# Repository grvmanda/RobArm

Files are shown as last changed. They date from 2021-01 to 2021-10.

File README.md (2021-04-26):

# RobArm

potential 6 DOF (maybe lower) 3D printed robotic arm. 

The repo is very rudimentary at the moment (CAD stored on Fusion 360's cloud); the code is based on ROS melodic.
The target platform is RPi4.

Custom stepper motor driver board (and boards for limit switches) designed on KiCad are also stored on this repo.

preview of rev 1 driver board: 

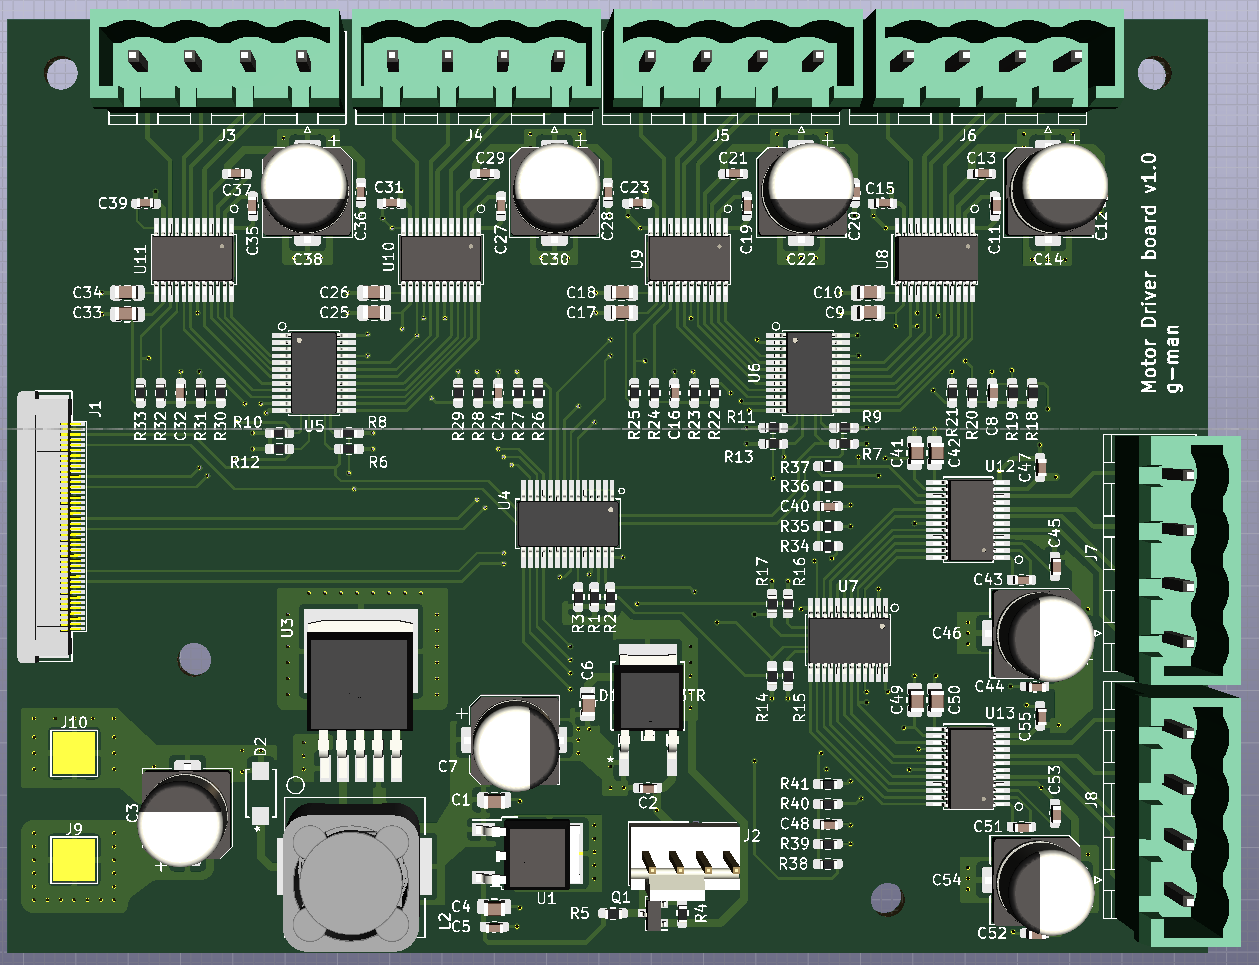
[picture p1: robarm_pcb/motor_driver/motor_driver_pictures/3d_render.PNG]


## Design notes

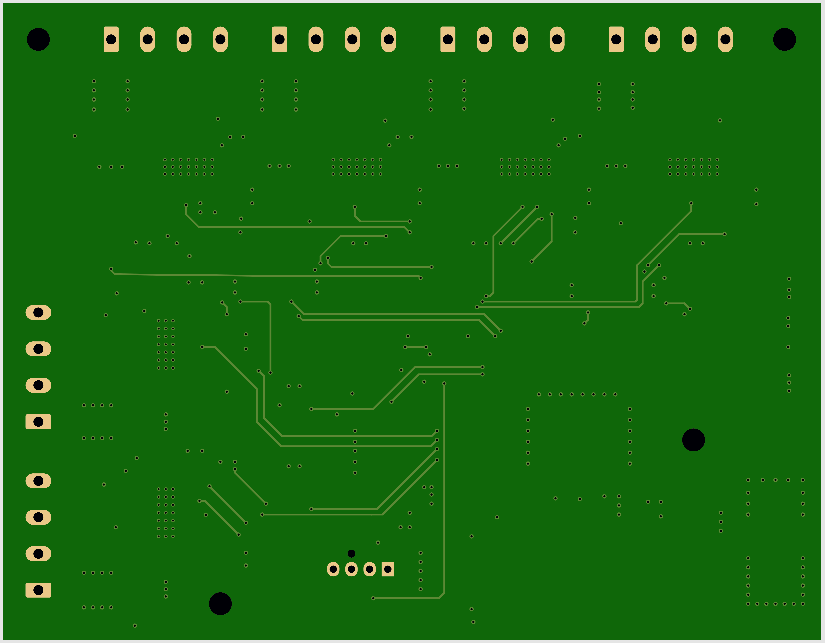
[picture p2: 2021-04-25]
robarm_pcb/motor_driver/motor_driver_pictures/back.PNG

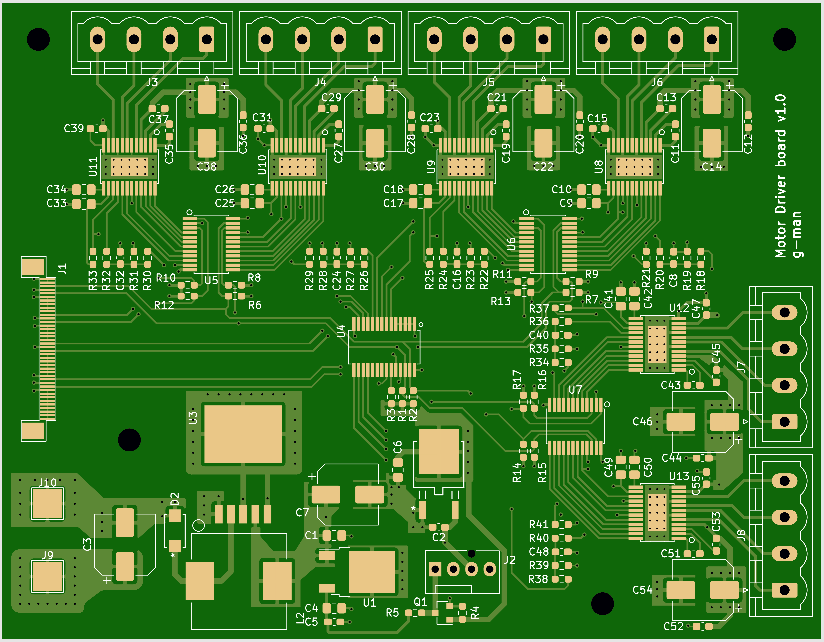
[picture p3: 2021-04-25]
robarm_pcb/motor_driver/motor_driver_pictures/front.PNG

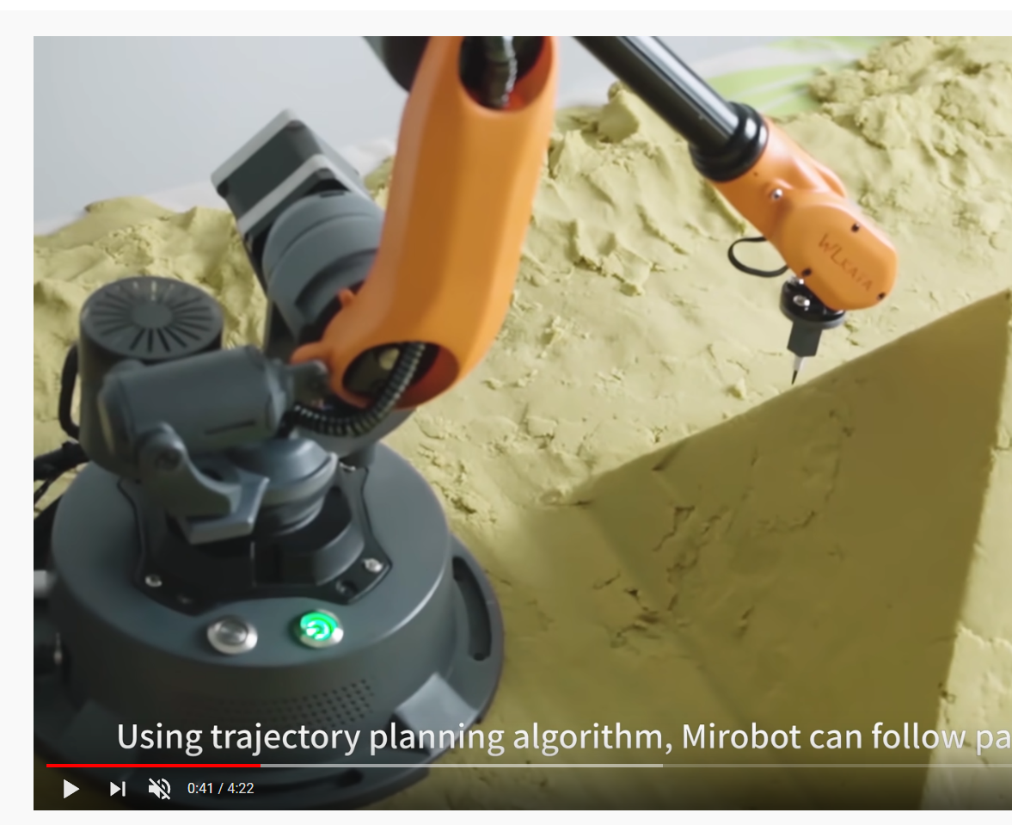
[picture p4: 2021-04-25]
robarm_documents/good reads/mirobot.png

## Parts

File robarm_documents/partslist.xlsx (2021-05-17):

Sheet: Template
 |  |  | Total |  | $0.00
Part Function | Part Number | Description | Unit Cost | Quantity | Total Cost | Link

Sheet: Motor Driver PCB
 |  |  | Total |  | $102.20
Part Function | Part Number | Description | Unit Cost | Quantity | Total Cost | Link
Power Management
12V PMIC | LM2576S-12/NOPB-ND | IC REG BUCK 12V 3A TO263-5 | $2.94 | 2 | $5.88 | https://www.digikey.com/en/products/detail/texas-instruments/LM2576S-12-NOPB/363651
3.3V PMIC | LD1117DT33TR | IC REG LINEAR 3.3V 800MA DPAK | $0.51 | 2 | $1.02 | https://www.digikey.com/en/products/detail/stmicroelectronics/LD1117DT33TR/585760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
5V | MC78M05BDTRKGOSCT-ND | IC REG LINEAR 5V 500MA DPAK | $0.53 | 2 | $1.06 | https://www.digikey.com/en/products/detail/on-semiconductor/MC78M05BDTRKG/919369
diodes | B340-13-F | DIODE SCHOTTKY 40V 3A SMC | $0.37 | 4 | $1.48 | https://www.digikey.com/en/products/detail/diodes-incorporated/B340-13-F/768768
Inductor for 3.3V PMIC | SRR1280A-101M | FIXED IND 100UH 2.1A 150MOHM SMD | $1.39 | 2 | $2.78 | https://www.digikey.com/en/products/detail/bourns-inc/SRR1280A-101M/4340250
 |  |  |  |  | $0.00
 |  |  |  |  | $0.00
Other ICs |  |  |  |  | $0.00
IO expansion | 296-25130-1-ND | IC I/O EXPANDER I2C 16B TSSOP | $1.61 | 5 | $8.05 | https://www.digikey.com/en/products/detail/texas-instruments/TCA9539PWR/2139129
PWM expansion | 568-11925-1-ND | IC LED DRVR LIN DIM 25MA 28TSSOP | $2.40 | 2 | $4.80 | https://www.digikey.com/en/products/detail/nxp-usa-inc/PCA9685PW-118/2034325
motor drivers | 296-45437-1-ND | IC MTR DRV BIPOLR 8-37V 24HTSSOP | $3.76 | 8 | $22.56 | https://www.digikey.com/en/products/detail/texas-instruments/DRV8886PWPR/6695811
level shifter FET | BSS138CT-ND | MOSFET N-CH 50V 220MA SOT23-3 | $0.28 | 5 | $1.40 | https://www.digikey.com/en/products/detail/on-semiconductor/BSS138/244210
 |  |  |  |  | $0.00
 |  |  |  |  | $0.00
Capacitors |  |  |  |  | $0.00
Driver VM caps | A768KE107M1VLAE036 | CAP ALUM POLY 100UF 20% 35V SMD | $0.68 | 7 | $4.76 | https://www.digikey.com/en/products/detail/kemet/A768KE107M1VLAE036/13420090
3.3V PMIC Cap | RHS0J102MCN1GS | CAP ALUM POLY 1000UF 6.3V SMD | $1.14 | 2 | $2.28 | https://www.digikey.com/en/products/detail/nichicon/RHS0J102MCN1GS/2209464
0.1uF Cap (Generic) 0603 | C0603C104M5RACTU | CAP CER 0.1UF 50V X7R 0603 | $0.02 | 50 | $0.97 | https://www.digikey.com/en/products/detail/kemet/C0603C104M5RACTU/2199782
10uF Cap (Generic) 0805 | GRM21BR61H106KE43L | CAP CER 10UF 50V X5R 0805 | $0.26 | 10 | $2.64 | https://www.digikey.com/en/products/detail/murata-electronics/GRM21BR61H106KE43L/10326316
0.47uF Cap (Generic) 0805 | CL21B474KBFNNNG | CAP CER 0.47UF 50V X7R 0805 | $0.04 | 50 | $1.90 | https://www.digikey.com/en/products/detail/samsung-electro-mechanics/CL21B474KBFNNNG/3894539
0.01uF Cap (Generic) 0603 | 06035C103JAT2A | CAP CER 10000PF 50V X7R 0603 | $0.04 | 50 | $1.93 | https://www.digikey.com/en/products/detail/avx-corporation/06035C103JAT2A/1600025
0.022uF Cap (Generic) 0603 | CL10B223KB8NNNC | CAP CER 0.022UF 50V X7R 0603 | $0.02 | 50 | $1.01 | https://www.digikey.com/en/products/detail/samsung-electro-mechanics/CL10B223KB8NNNC/3886762
0.22uF Cap (Generic) 0603 | CC0603ZRY5V9BB224 | CAP CER 0.22UF 50V Y5V 0603 | $0.09 | 10 | $0.86 | https://www.digikey.com/en/products/detail/yageo/CC0603ZRY5V9BB224/5195237
 |  |  |  |  | $0.00
 |  |  |  |  | $0.00
Resistors |  |  |  |  | $0.00
1k Res (Generic) 0603 | RC0603JR-7W1KL | RES 1K OHM 5% 1/5W 0603 | $0.03 | 20 | $0.60 | https://www.digikey.com/en/products/detail/yageo/RC0603JR-7W1KL/12698826
10k Res (Generic) 0603 0.1W | CRGCQ0603F10K | CRGCQ 0603 10K 1% | $0.01 | 100 | $1.26 | https://www.digikey.com/en/products/detail/te-connectivity-passive-product/CRGCQ0603F10K/8576302
20k Res (Generic) 0603 0.1W | RC0603JR-0720KL | RES SMD 20K OHM 5% 1/10W 0603 | $0.01 | 100 | $0.80 | https://www.digikey.com/en/products/detail/yageo/RC0603JR-0720KL/726740
30k Res (Generic) 0603 0.1W | AC0603JR-0730KL | RES SMD 30K OHM 5% 1/10W 0603 | $0.01 | 100 | $0.97 | https://www.digikey.com/en/products/detail/yageo/AC0603JR-0730KL/5896432
 |  |  |  |  | $0.00
 |  |  |  |  | $0.00
Connectors, Misc |  |  |  |  | $0.00
Fan connector | 470533000 | CONN HEADER VERT 4POS 2.54MM | $0.48 | 2 | $0.96 | https://www.digikey.com/en/products/detail/molex/0470533000/3262217
FPC to RPI | ZF5S-40-01-T-WT | CONN FFC BOTTOM 40POS 0.50MM R/A | $2.55 | 4 | $10.20 | https://www.digikey.com/en/products/detail/samtec-inc/ZF5S-40-01-T-WT/4822887
FPC adapter board | 1528-1096-ND | FPC ADAPTER 50PIN 0.5MM PITCH | $2.95 | 2 | $5.90 | https://www.digikey.com/en/products/detail/adafruit-industries-llc/1492/5154671
4" FFC cable | AE11342-ND | CABLE FFC 40POS 0.50MM 4" | $2.25 | 1 | $2.25 | https://www.digikey.com/en/products/detail/assmann-wsw-components/AFFC-050-40-102-11/6570363
6" FFC cable | WM19594-ND | CABLE FFC 40POS 0.50MM 6" | $2.66 | 1 | $2.66 | https://www.digikey.com/en/products/detail/molex/0151660436/3281317
Optical Sensor | OR626-ND | SENSOR OPT SLOT PHOTOTRAN PCB MT | $3.08 | 2 | $6.16 | https://www.digikey.com/en/products/detail/omron-electronics-inc-emc-div/EE-SX1071/274425
base limit switch to board | WM15254-ND | PICOBLADE 3 CIRCUIT 150MM | $2.53 | 1 | $2.53 | https://www.digikey.com/en/products/detail/molex/0151340302/6198144?s=N4IgTCBcDaIIwFY4GYAsAGZ6IF0C%2BQA
Connector Header 3 pos | WM1732-ND | CONN HEADER VERT 3POS 1.25MM | $0.24 | 5 | $2.53 | https://www.digikey.com/en/products/detail/molex/0530470310/242854
 |  |  |  |  | $0.00
 |  |  |  |  | $0.00
 |  |  |  |  | $0.00
 |  |  |  |  | $0.00
 |  |  |  |  | $0.00
 |  |  |  |  | $0.00
 |  |  |  |  | $0.00

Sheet: TMC2130 Based Board
 |  |  | Total |  | $0.00
Part Function | Part Number | Description | Unit Cost | Quantity | Total Cost | Link

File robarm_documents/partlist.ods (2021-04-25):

 |  |  |  | Total | $125.53
Part Function | Part Number | Description | Unit Cost | Quantity | Total Cost | Link
Robot Base Mechanical, etc
Nema-17 | 17HS19-1684S-PG51 | Base motor | $29.46 | 1 | $29.46 | https://www.omc-stepperonline.com/nema-17-stepper-motor-bipolar-l48mm-w-gear-raio-511-planetary-gearbox-17hs19-1684s-pg51.html
Ball Bearing | 6806-2RS | 30mm x 42mm x 7mm (set of 2) | $6.49 | 1 | $6.49 | https://www.amazon.com/gp/product/B082PYMKLG/ref=ppx_yo_dt_b_asin_title_o00_s00?ie=UTF8&psc=1
Thrust Bearing | 51107 | 35mm x 52mm x 12mm (set of 2) | $9.99 | 1 | $9.99 | https://www.amazon.com/gp/product/B07G847G75/ref=ppx_yo_dt_b_asin_title_o00_s00?ie=UTF8&psc=1
Noctua fan | NF-A4x10 PWM | 40mm x 10mm | $13.95 | 1 | $13.95 | https://www.amazon.com/dp/B07DXRNYNX/ref=emc_b_5_t
 |  |  |  |  | $0.00
Robot Base Electrical
Base PCB
Phoenix connectors | 1753479, 1751086 | 0.2inch 4 pin male and female connectors (set of 10) | $8.88 | 1 | $8.88 | https://www.amazon.com/Willwin-4-Pin-5-08mm-Female-Terminal/dp/B07796625D
motor drivers | DRV8886 | IC MTR DRV BIPOLR 8-37V 24HTSSOP | $3.76 | 6 | $22.56 | https://www.digikey.com/en/products/detail/texas-instruments/DRV8886PWPR/6695811
IO expansion | TCA9539 | IC I/O EXPANDER I2C 16B TSSOP | $1.61 | 3 | $4.83 | https://www.digikey.com/en/products/detail/texas-instruments/TCA9539PWR/2139129
PWM expansion | PCA9685 | IC LED DRVR LIN DIM 25MA 28TSSOP | $2.40 | 1 | $2.40 | https://www.digikey.com/en/products/detail/nxp-usa-inc/PCA9685PW-118/2034325
3.3V PMIC | LM2576SX-3.3/NOPB | IC REG BUCK 3.3V 3A TO263-5 | $2.94 | 0 | $0.00 | https://www.digikey.com/en/products/detail/texas-instruments/LM2576SX-3-3-NOPB/366792
Driver VM caps | A768KE107M1VLAE036 | CAP ALUM POLY 100UF 20% 35V SMD | $0.68 | 7 | $4.76 | https://www.digikey.com/en/products/detail/kemet/A768KE107M1VLAE036/13420090
3.3V PMIC Cap | RHS0J102MCN1GS | CAP ALUM POLY 1000UF 6.3V SMD | $1.14 | 1 | $1.14 | https://www.digikey.com/en/products/detail/nichicon/RHS0J102MCN1GS/2209464
Inductor for 3.3V PMIC | SRR1280A-101M | FIXED IND 100UH 2.1A 150MOHM SMD | $1.39 | 1 | $1.39 | https://www.digikey.com/en/products/detail/bourns-inc/SRR1280A-101M/4340250
50-pin FPC board for RPI | 1528-1096-ND | FPC ADAPTER 50PIN 0.5MM PITCH | $2.95 | 1 | $2.95 | https://www.digikey.com/en/products/detail/adafruit-industries-llc/1492/5154671
FPC to RPI | ZF5S-40-01-T-WT | CONN FFC BOTTOM 40POS 0.50MM R/A | $2.55 | 2 | $5.10 | https://www.digikey.com/en/products/detail/samtec-inc/ZF5S-40-01-T-WT/4822887
12V PMIC | LM2576S-12/NOPB-ND | IC REG BUCK 12V 3A TO263-5 | $2.94 | 0 | $0.00 | https://www.digikey.com/en/products/detail/texas-instruments/LM2576S-12-NOPB/363651
5V | MC78M05BDTRKG | IC REG LINEAR 5V 500MA DPAK | $0.49 | 1 | $0.49 | https://www.digikey.com/en/products/detail/on-semiconductor/MC78M05BDTRKG/919369
diodes | B340-13-F | DIODE SCHOTTKY 40V 3A SMC | $0.37 | 2 | $0.74 | https://www.digikey.com/en/products/detail/diodes-incorporated/B340-13-F/768768
3.3V PMIC | LD1117DT33TR | IC REG LINEAR 3.3V 800MA DPAK | $0.51 | 1 | $0.51 | https://www.digikey.com/en/products/detail/stmicroelectronics/LD1117DT33TR/585760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
Limit Switch PCB
Limit switch | D2FS-F-N-A | SWITCH SNAP ACT SPST-NO 100MA 6V |  |  | $0.00
Optical Sensor | OR626-ND | SENSOR OPT SLOT PHOTOTRAN PCB MT | $3.08 | 2 | $6.16 | https://www.digikey.com/en/products/detail/omron-electronics-inc-emc-div/EE-SX1071/274425
 |  |  |  |  | $0.00
Cable Assemblies
base limit switch to board | WM15254-ND | PICOBLADE 3 CIRCUIT 150MM | $2.53 | 1 | $2.53 | https://www.digikey.com/en/products/detail/molex/0151340302/6198144?s=N4IgTCBcDaIIwFY4GYAsAGZ6IF0C%2BQA
Connector Header 3 pos | WM1732-ND | CONN HEADER VERT 3POS 1.25MM | $0.24 | 5 | $1.20 | https://www.digikey.com/en/products/detail/molex/0530470310/242854
 |  |  |  |  | $0.00
 |  |  |  |  | $0.00
 |  |  |  |  | $0.00
 |  |  |  |  | $0.00
 |  |  |  |  | $0.00

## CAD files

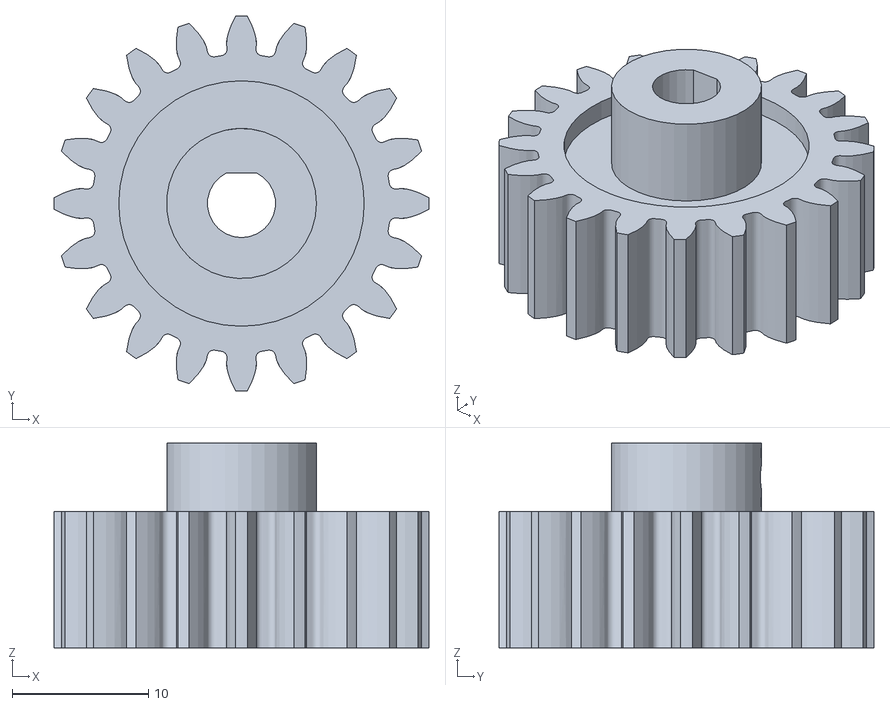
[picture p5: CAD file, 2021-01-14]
robarm_cad/nema17/second_draft.stl
27.5 x 27.5 x 15.0

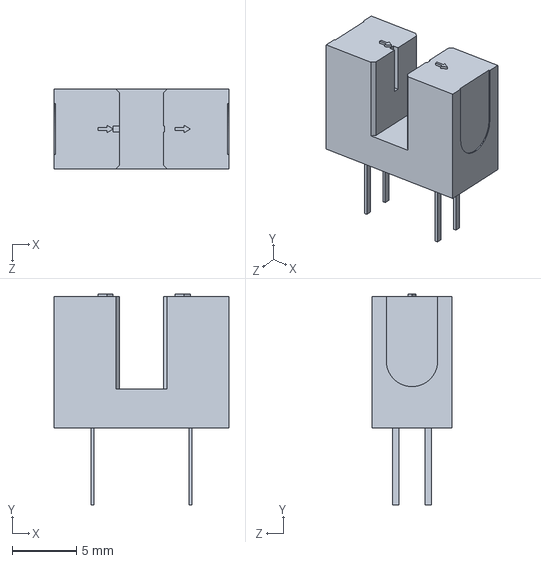
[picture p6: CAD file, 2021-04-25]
robarm_pcb/kicad_libraries/3dmodels/ul_EESX1071/STEP/EE_SX1071.step
13.6 x 16.4 x 6.20 mm

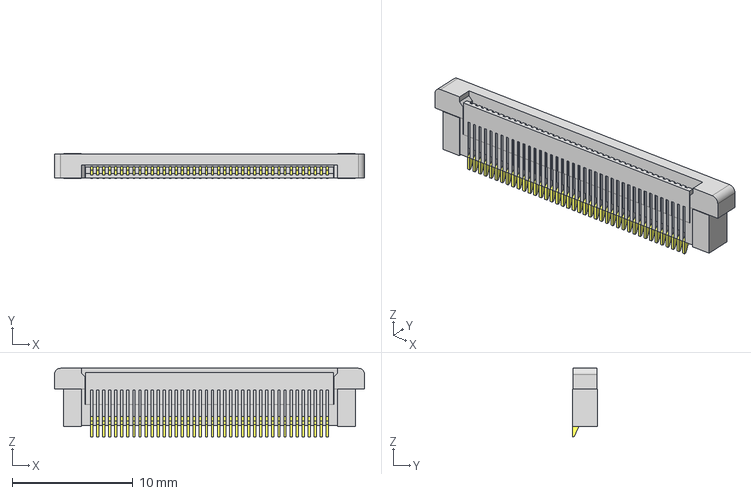
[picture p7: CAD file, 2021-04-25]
robarm_pcb/kicad_libraries/3dmodels/ZF5S-40-01-T-WT.stp
25.6 x 2.10 x 5.67 mm
_ZF5S-40-01-WT_socket
_C-297-40-01_pins

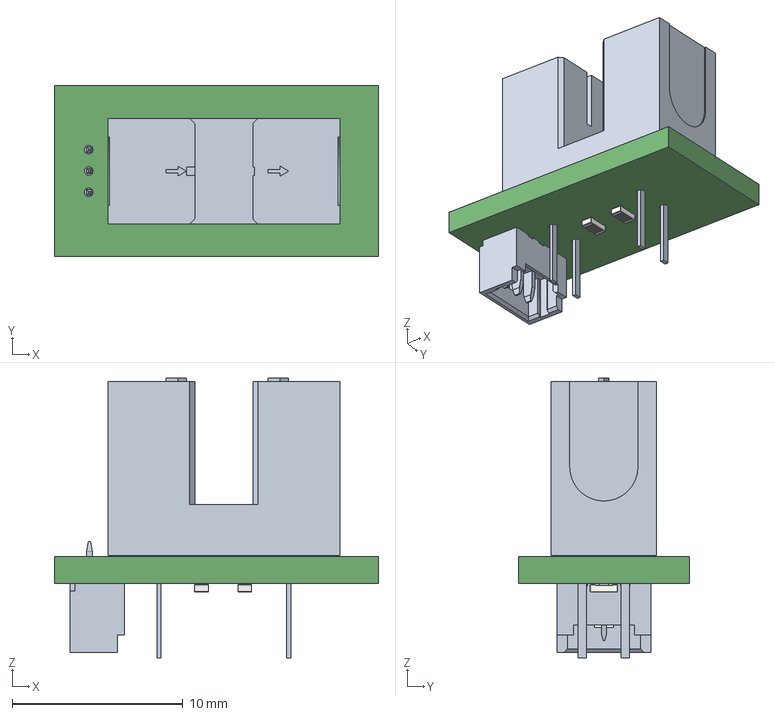
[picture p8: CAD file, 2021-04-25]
robarm_pcb/motor_driver/limit_switch_prj/limit_switch_prj/limit_switch_prj.step
19.0 x 10.0 x 16.4 mm

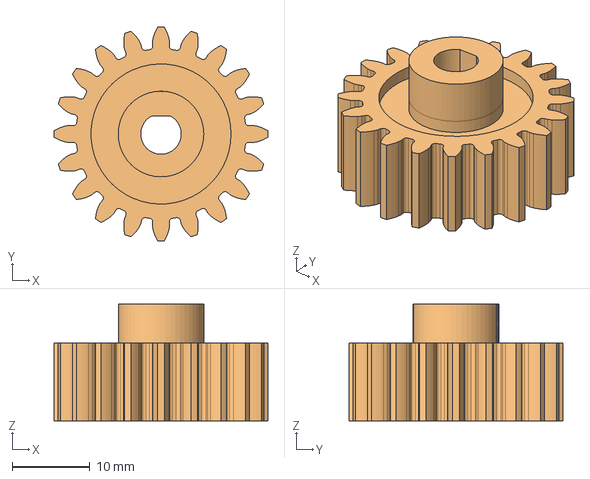
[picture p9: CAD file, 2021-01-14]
robarm_cad/nema17/spur_gear.FCStd
27.5 x 27.5 x 15.0 mm

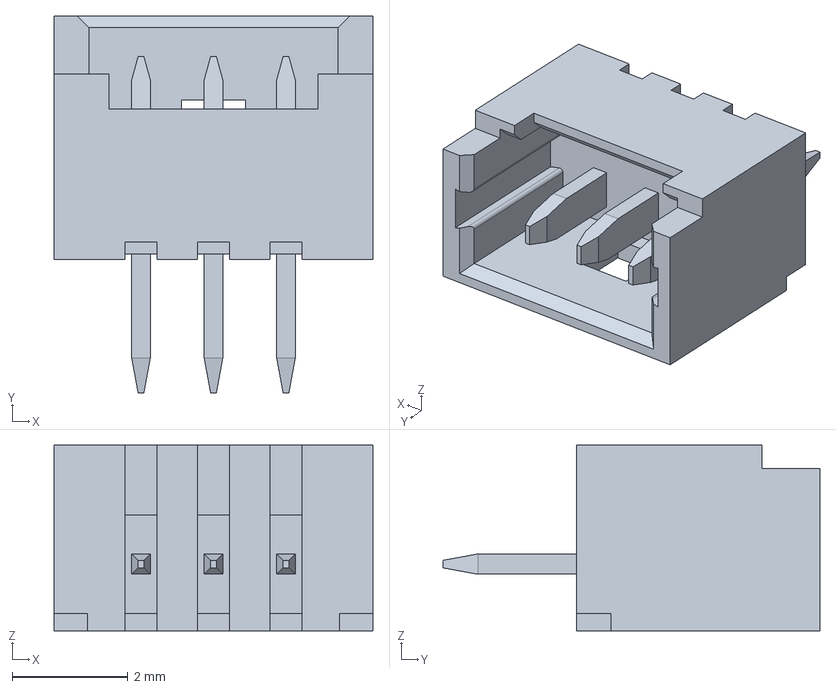
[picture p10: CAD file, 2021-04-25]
robarm_pcb/kicad_libraries/3dmodels/53047-0310_stp/530470310.stp
5.50 x 6.50 x 3.20 mm

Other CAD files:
robarm_pcb/motor_driver/limit_switch_prj/limit_switch_prj/limit_switch_prj v1.stl

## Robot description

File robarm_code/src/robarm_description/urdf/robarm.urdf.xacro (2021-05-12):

<?xml version="1.0"?>
<robot name="robarm" xmlns:xacro="http://ros.org/wiki/xacro">

  <!-- Import Rviz colors -->
  <xacro:include filename="$(find robarm_description)/urdf/materials.xacro" />

  <!-- Transmission macro -->
  <xacro:macro name="SimpleTransmission" params="joint n">
    <transmission name="tran${n}">
      <type>transmission_interface/SimpleTransmission</type>
      <joint name="${joint}">
        <hardwareInterface>hardware_interface/EffortJointInterface</hardwareInterface>
      </joint>
      <actuator name="motor${n}">
        <hardwareInterface>hardware_interface/EffortJointInterface</hardwareInterface>
        <mechanicalReduction>1</mechanicalReduction>
      </actuator>
    </transmission>
  </xacro:macro>

  <!-- World -->
  <link name="world">
  </link>

  <!-- World fixed joint-->
  <joint name="world_fixed" type="fixed">
    <origin xyz="0 0 0" rpy="0 0 0"/>
    <parent link="world"/>
    <child link="link1"/>
  </joint>

  <!-- Link 1 -->
  <link name="link1">
    <visual>
      <origin xyz="0 0 0.1" rpy="0 0 0"/>
      <!-- fix geometry later -->
      <geometry>
        <box size="0.4 0.4 0.2"/>
      </geometry>
      <material name="black"/>
    </visual>

    <collision>
      <origin xyz="0 0 0.1" rpy="0 0 0"/>
      <geometry>
        <cylinder radius="0.4" length="0.2"/>
      </geometry>
    </collision>

    <!-- inertia is not correct - change this later -->
    <inertial>
      <!-- <origin xyz="0 0 0" /> -->
      <mass value="0.1" />
      <inertia ixx="0.001" ixy="0.0" ixz="0.0" iyy="0.001" iyz="0.0" izz="0.001" />
    </inertial>
  </link>

  <!-- Joint 1 -->
  <joint name="joint1" type="revolute">
    <parent link="link1"/>
    <child link="link2"/>
    <origin xyz="0.0 0.0 0.2" rpy="0 0 0"/>
    <axis xyz="0 0 1"/>
    <limit velocity="4.8" effort="1" lower="${-pi*0.9}" upper="${pi*0.9}" />
  </joint>

  <!-- Transmission 1 -->
  <xacro:SimpleTransmission n="1" joint="joint1" />

  <!--  Link 2 -->
  <link name="link2">
    <visual>
      <origin xyz="0 0 0.3" rpy="0 0 0"/>
      <geometry>
        <box size="0.1 0.1 0.6"/>
      </geometry>
      <material name="orange"/>
    </visual>

    <collision>
      <origin xyz="0 0 0.6" rpy="0 0 0"/>
      <geometry>
        <cylinder radius="0.1" length="0.6"/>
      </geometry>
    </collision>

   <inertial>
      <!-- <origin xyz="0 0 0" /> -->
      <mass value="0.1" />
      <inertia ixx="0.001" ixy="0.0" ixz="0.0" iyy="0.001" iyz="0.0" izz="0.001" />
    </inertial>

  </link>

  <!-- Joint 2 -->
  <joint name="joint2" type="revolute">
    <parent link="link2"/>
    <child link="link3"/>
    <origin xyz="0.0 0.0 0.6" rpy="0 0 0"/>
    <axis xyz="0 1 0"/>
    <limit velocity="4.8" effort="1" lower="${-pi*0.9}" upper="${pi*0.9}" />
  </joint>

  <!-- Transmission 2 -->
  <xacro:SimpleTransmission n="2" joint="joint2" />

  <!--  Link 3 -->
  <link name="link3">
    <visual>
      <origin xyz="0 0 0.3" rpy="0 0 0"/>
      <geometry>
        <box size="0.1 0.1 0.6"/>
      </geometry>
      <material name="grey"/>
    </visual>

    <collision>
      <origin xyz="0 0 0.6" rpy="0 0 0"/>
      <geometry>
        <cylinder radius="0.1" length="0.6"/>
      </geometry>
    </collision>

   <inertial>
      <!-- <origin xyz="0 0 0" /> -->
      <mass value="0.1" />
      <inertia ixx="0.001" ixy="0.0" ixz="0.0" iyy="0.001" iyz="0.0" izz="0.001" />
    </inertial>

  </link>

  <!-- Joint 3 -->
  <joint name="joint3" type="revolute">
    <parent link="link3"/>
    <child link="link4"/>
    <origin xyz="0.0 0.0 0.6" rpy="0 0 0"/>
    <axis xyz="1 0 0"/>
    <limit velocity="4.8" effort="1" lower="${-pi*0.9}" upper="${pi*0.9}" />
  </joint>

  <!-- Transmission 3 -->
  <xacro:SimpleTransmission n="3" joint="joint3" />

  <!--  Link 4 -->
  <link name="link4">
    <visual>
      <origin xyz="0 0 0.3" rpy="0 0 0"/>
      <geometry>
        <box size="0.1 0.1 0.6"/>
      </geometry>
      <material name="brown"/>
    </visual>

    <collision>
      <origin xyz="0 0 0.6" rpy="0 0 0"/>
      <geometry>
        <cylinder radius="0.1" length="0.6"/>
      </geometry>
    </collision>

   <inertial>
      <!-- <origin xyz="0 0 0" /> -->
      <mass value="0.1" />
      <inertia ixx="0.00" ixy="0.0" ixz="0.0" iyy="0.001" iyz="0.0" izz="0.001" />
    </inertial>

  </link>

  <gazebo>
    <plugin name="gazebo_ros_control" filename="libgazebo_ros_control.so">
      <robotNamespace>/robarm</robotNamespace>
      <robotSimType>gazebo_ros_control/DefaultRobotHWSim</robotSimType>
    </plugin>
  </gazebo>
  
</robot>

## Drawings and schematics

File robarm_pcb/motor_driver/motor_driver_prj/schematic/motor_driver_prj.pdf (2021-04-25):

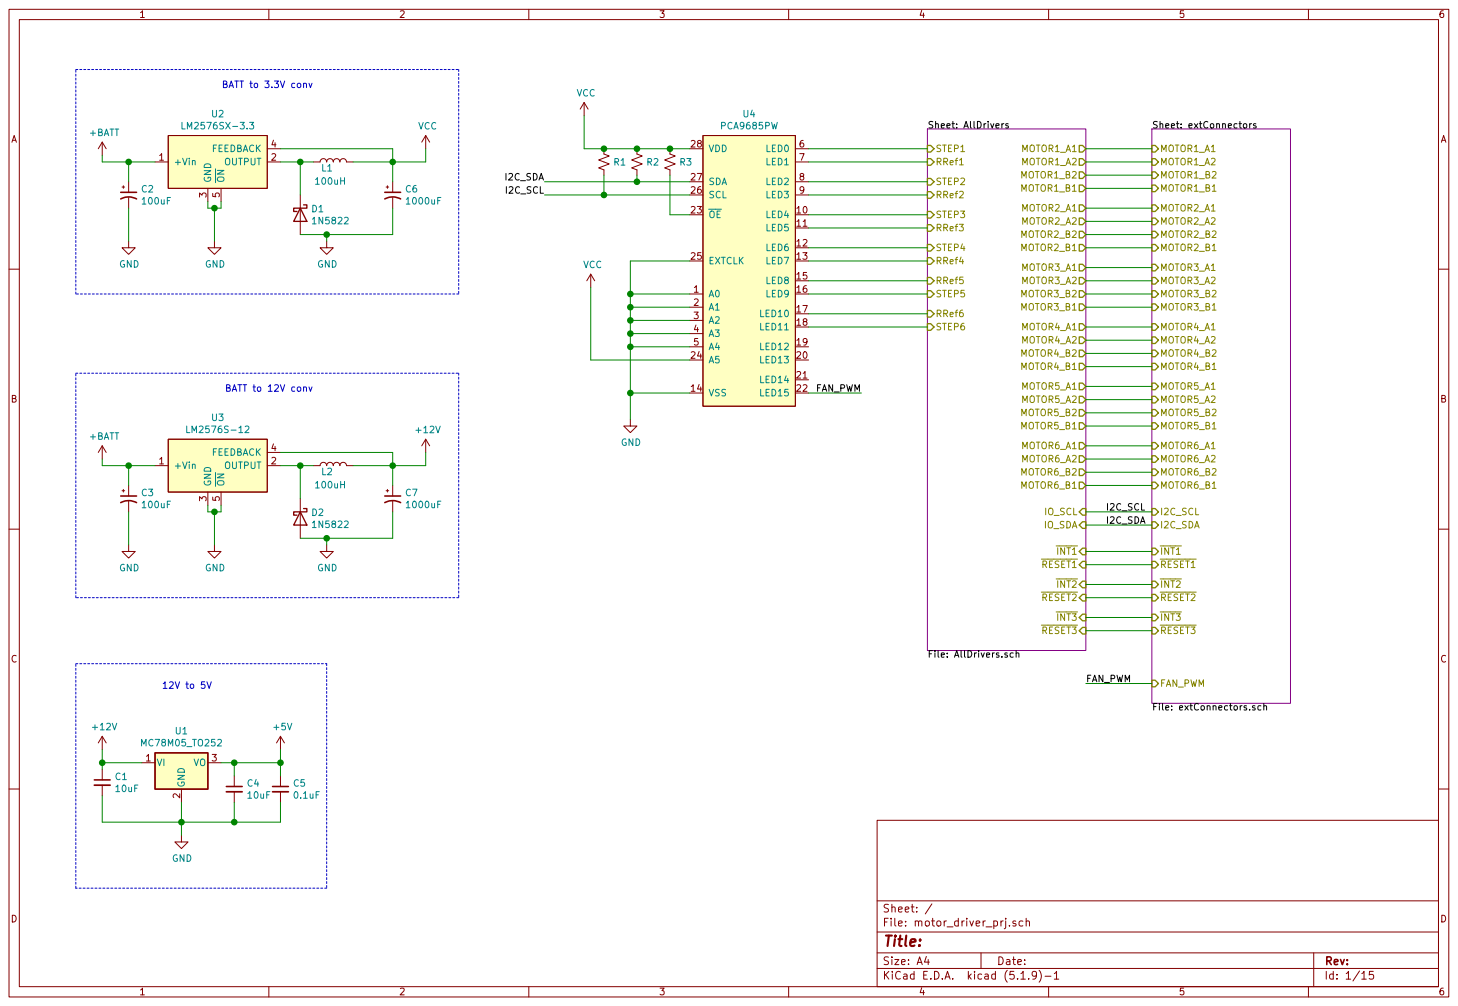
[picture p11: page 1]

Sheet: AllDrivers File: AllDrivers.sch
STEP1 RRef1 STEP2 RRef2 STEP3 RRef3 STEP4 RRef4 RRef6 STEP6 RRef5 STEP5

Sheet: extConnectors File: extConnectors.sch
MOTOR1_A1 MOTOR1_A2 MOTOR1_B2 MOTOR1_B1 MOTOR2_A1 MOTOR2_A2 MOTOR2_B2 MOTOR2_B1 MOTOR3_A1 MOTOR3_A2 MOTOR3_B2 MOTOR3_B1 MOTOR4_A1 MOTOR4_A2 MOTOR4_B2 MOTOR4_B1 MOTOR5_A1 MOTOR5_A2 MOTOR5_B2 MOTOR5_B1 MOTOR6_A1 MOTOR6_A2 MOTOR6_B2 MOTOR6_B1

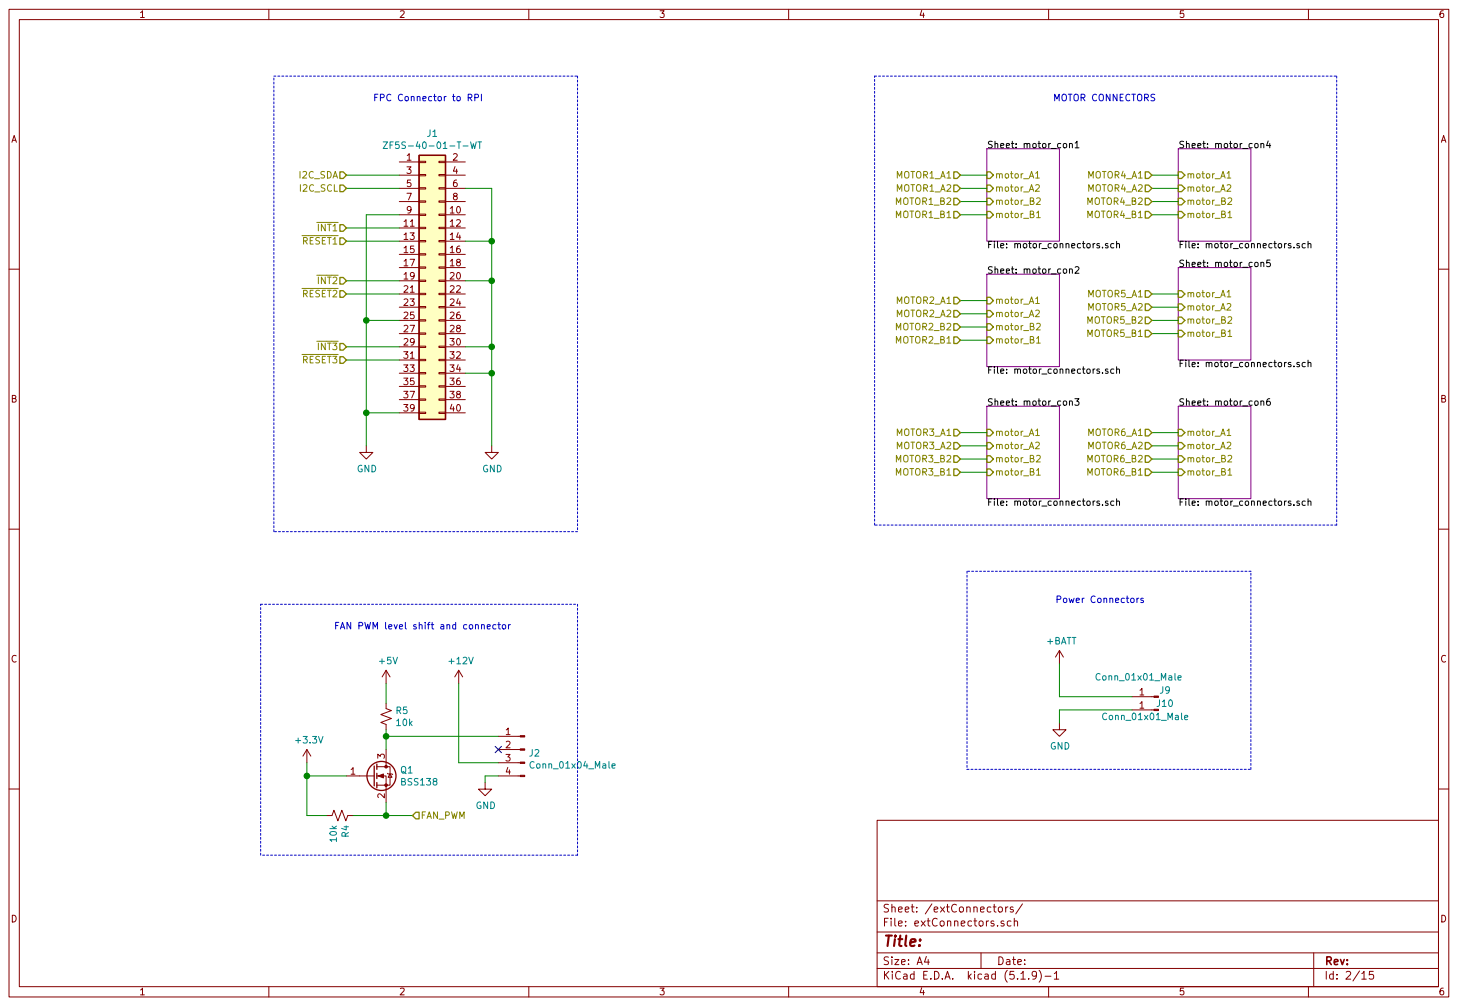
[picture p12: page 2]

Id: 2/15 Title: File: extConnectors.sch Sheet: /extConnectors/

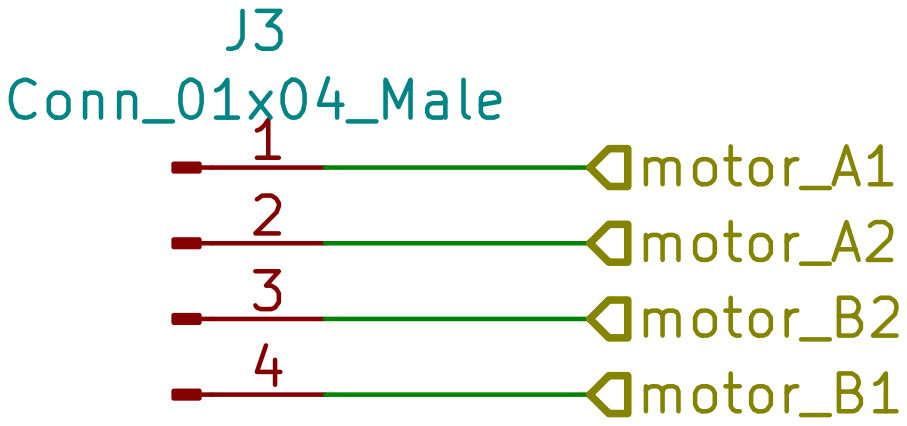
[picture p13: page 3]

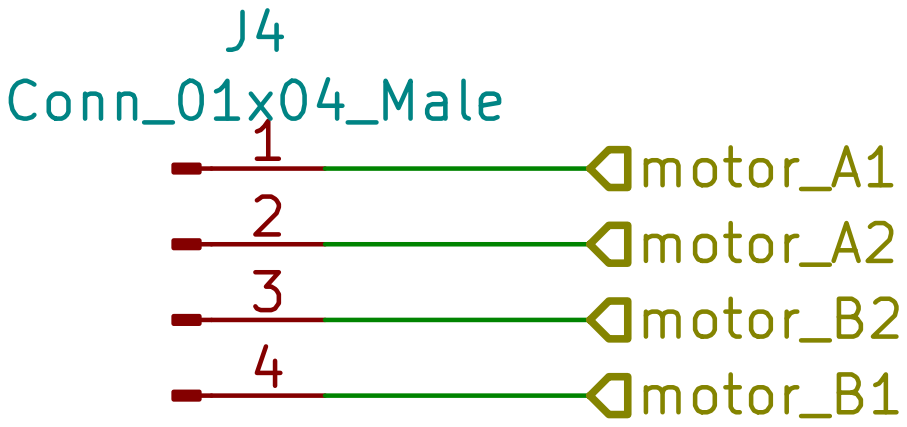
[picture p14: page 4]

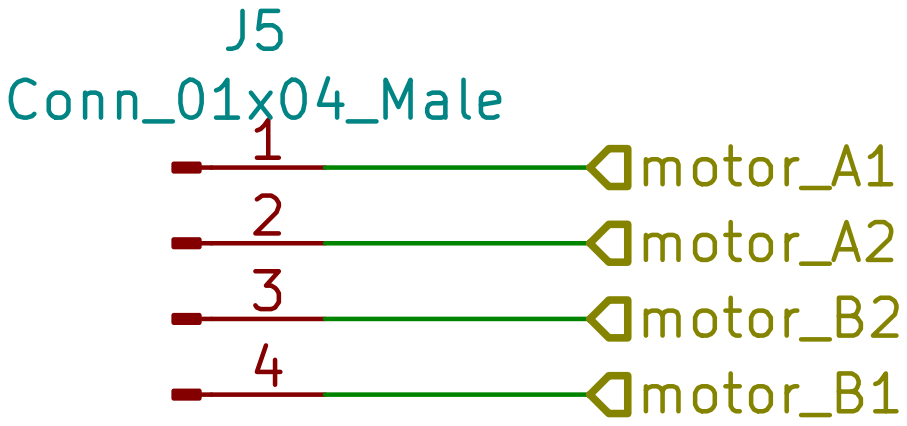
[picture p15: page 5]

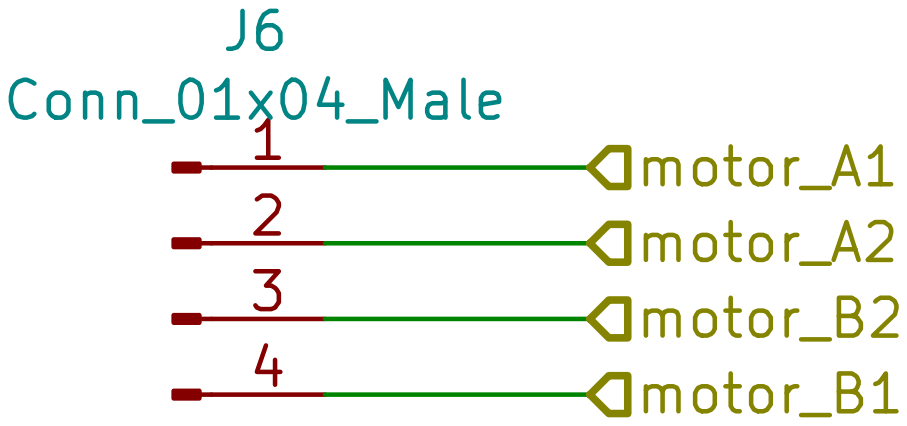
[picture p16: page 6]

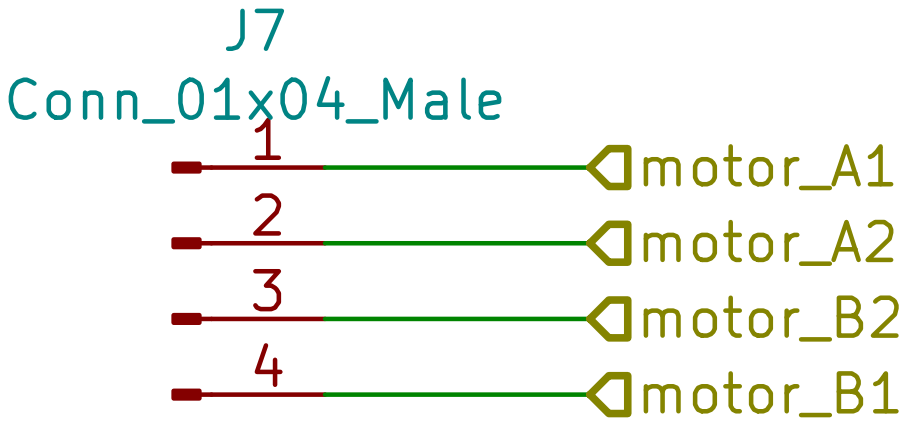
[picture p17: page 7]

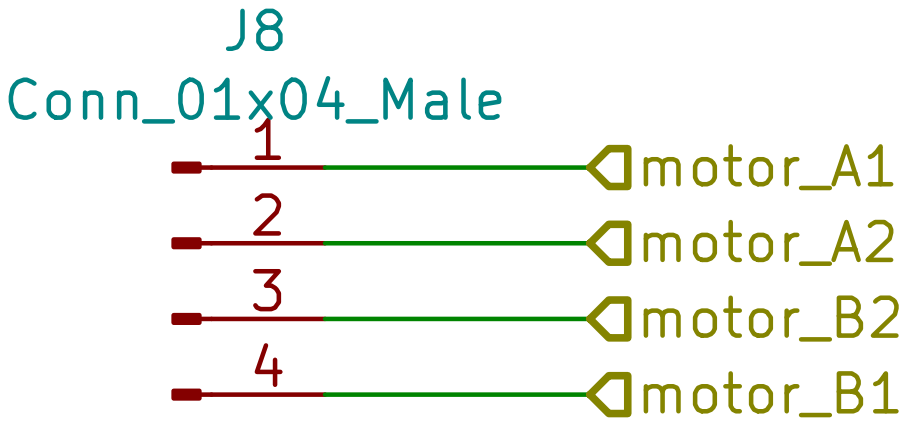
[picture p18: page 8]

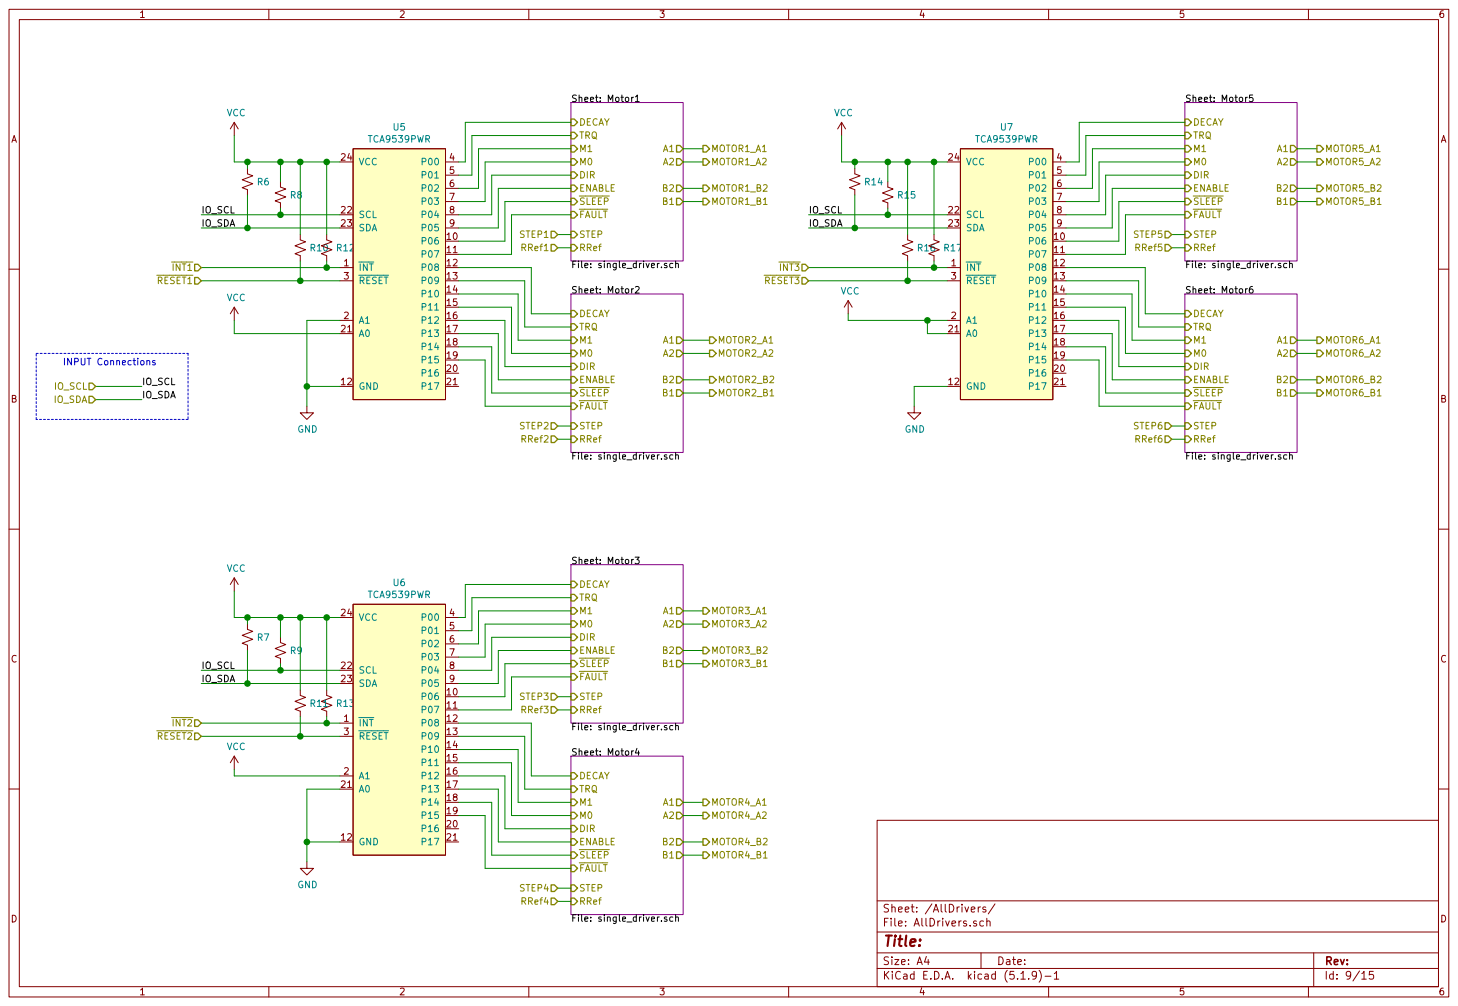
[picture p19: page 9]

A1A2B2B1 FAULT Sheet: Motor1 File: single_driver.sch RRef DECAY
TRQ M1 M0 DIR
A1A2B2B1 FAULT Sheet: Motor4 File: single_driver.sch RRef DECAY
A1A2B2B1 FAULT Sheet: Motor2 File: single_driver.sch RRef DECAY
A1A2B2B1 FAULT Sheet: Motor3 File: single_driver.sch RRef DECAY

Sheet: Motor5 File: single_driver.sch RRef DECAY
A1A2B2B1 FAULT Sheet: Motor6 File: single_driver.sch RRef DECAY

Id: 9/15 Title: File: AllDrivers.sch Sheet: /AllDrivers/

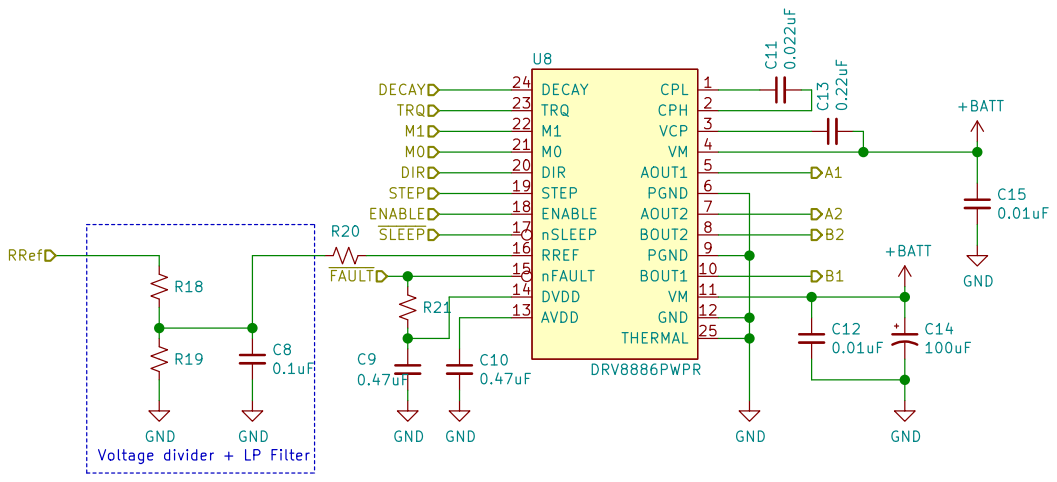
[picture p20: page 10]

File: single_driver.sch Sheet: /AllDrivers/Motor4/ GND

Voltage divider + LP Filter

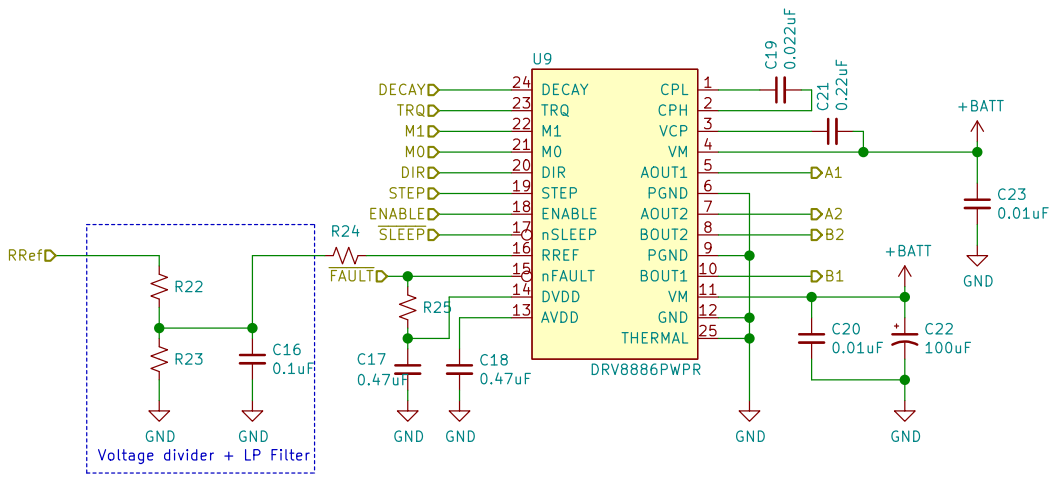
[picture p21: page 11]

File: single_driver.sch Sheet: /AllDrivers/Motor3/ GND

Voltage divider + LP Filter

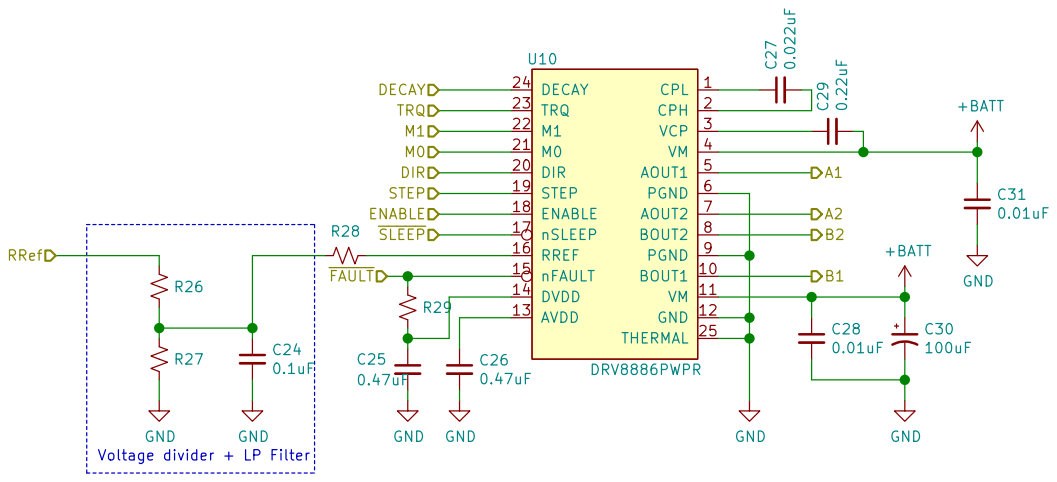
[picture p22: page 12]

File: single_driver.sch Sheet: /AllDrivers/Motor2/ GND

Voltage divider + LP Filter


File: single_driver.sch Sheet: /AllDrivers/Motor1/ GND

Voltage divider + LP Filter


File: single_driver.sch Sheet: /AllDrivers/Motor5/ GND

Voltage divider + LP Filter


File: single_driver.sch Sheet: /AllDrivers/Motor6/ GND

Voltage divider + LP Filter

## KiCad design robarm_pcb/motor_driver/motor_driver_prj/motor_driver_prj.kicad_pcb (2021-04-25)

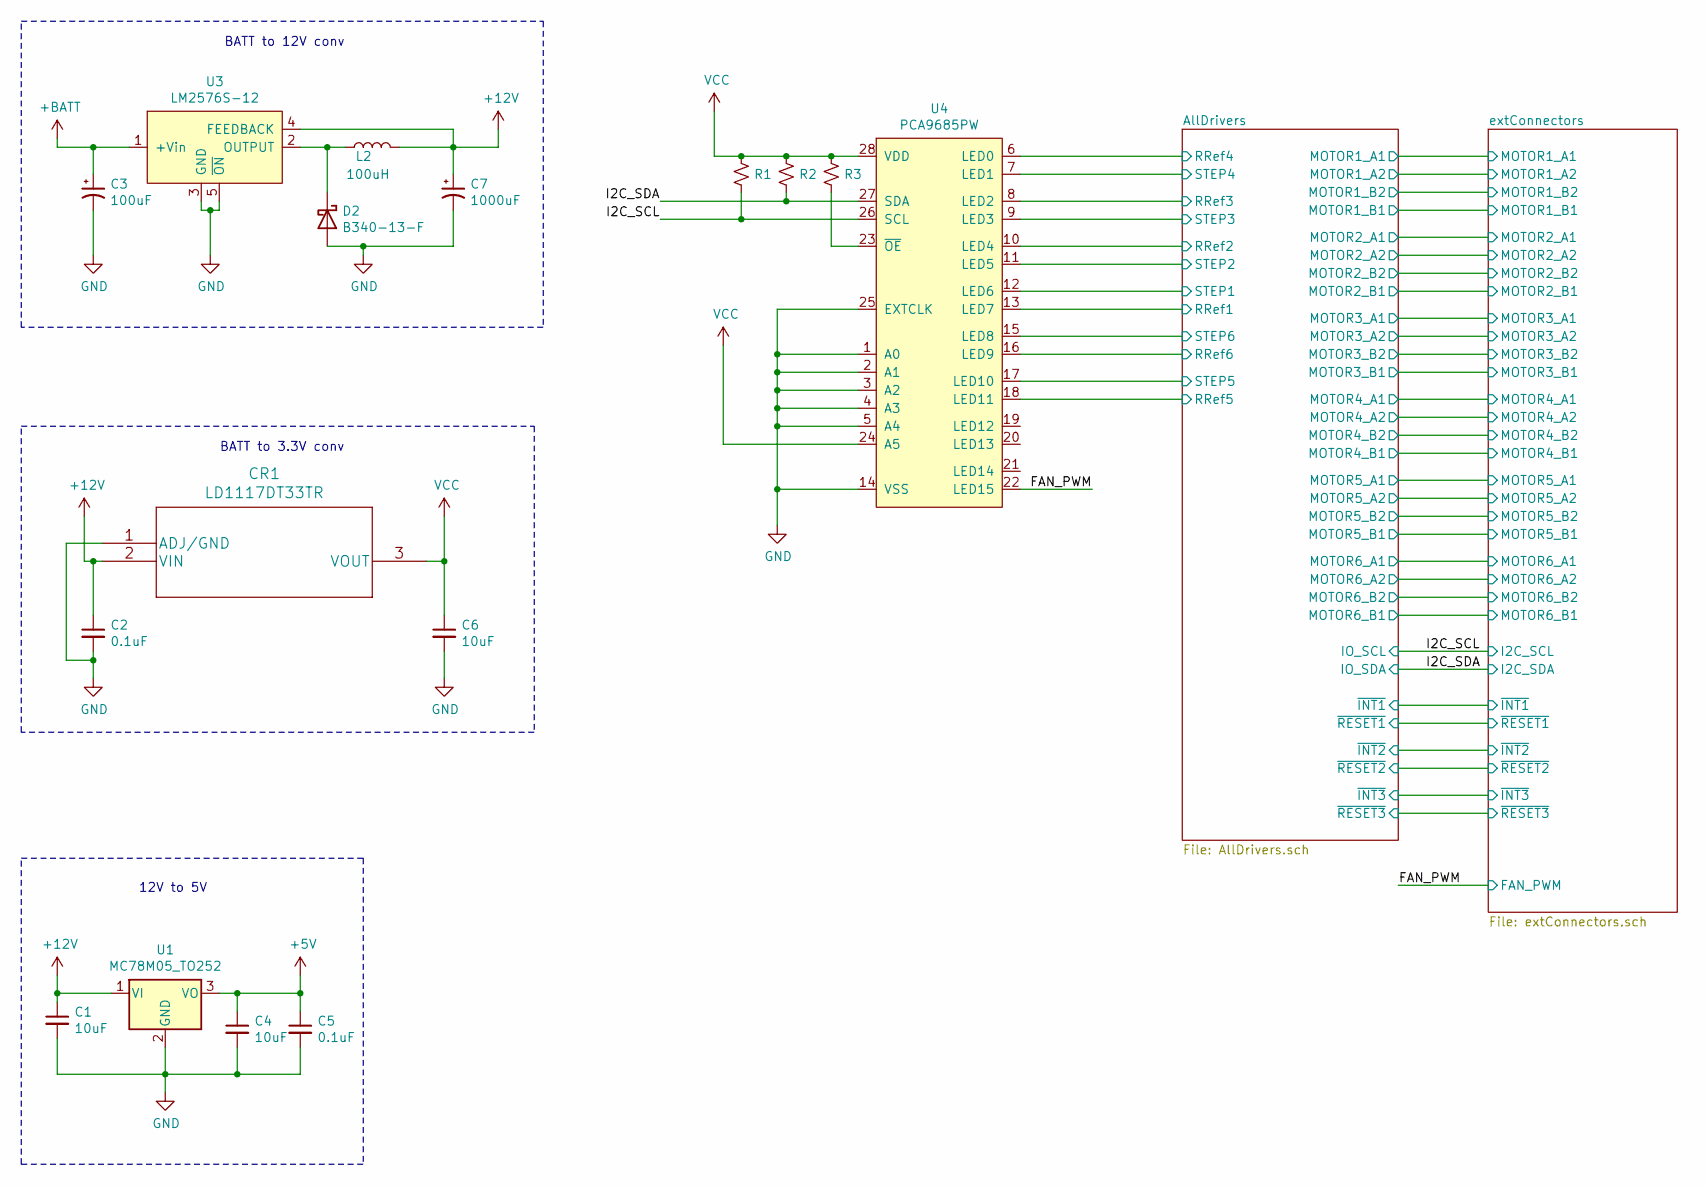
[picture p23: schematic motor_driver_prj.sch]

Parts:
C1, C4, C6: 10uF; C_0805_2012Metric_Pad1.18x1.45mm_HandSolder
C2, C5: 0.1uF; C_0603_1608Metric_Pad1.08x0.95mm_HandSolder
C3: 100uF; CP_Elec_8x6.2
C7: 1000uF; CP_Elec_8x6.2
CR1: LD1117DT33TR
D2: B340-13-F
L2: 100uH; SRR1280A-101M
R1, R2, R3: R_Small_US; R_0603_1608Metric_Pad0.98x0.95mm_HandSolder
U1: MC78M05_TO252; TO-252-2
U3: LM2576S-12; LM2576SX_TO263-5
U4: PCA9685PW; PC9685_TSSOP28

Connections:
+5V: C4.1, C5.1, U1.3 (VO); also elsewhere on the board
+12V: C1.1, C2.1, C7.1, CR1.2 (VIN), L2.2, U1.1 (VI), U3.4 (FEEDBACK); also elsewhere on the board
+BATT: C3.1, U3.1 (+Vin); also elsewhere on the board
/AllDrivers/RRef1: U4.13 (LED7); also elsewhere on the board
/AllDrivers/RRef2: U4.10 (LED4); also elsewhere on the board
/AllDrivers/RRef3: U4.8 (LED2); also elsewhere on the board
/AllDrivers/RRef4: U4.6 (LED0); also elsewhere on the board
/AllDrivers/RRef5: U4.18 (LED11); also elsewhere on the board
/AllDrivers/RRef6: U4.16 (LED9); also elsewhere on the board
/AllDrivers/STEP1: U4.12 (LED6); also elsewhere on the board
/AllDrivers/STEP2: U4.11 (LED5); also elsewhere on the board
/AllDrivers/STEP3: U4.9 (LED3); also elsewhere on the board
/AllDrivers/STEP4: U4.7 (LED1); also elsewhere on the board
/AllDrivers/STEP5: U4.17 (LED10); also elsewhere on the board
/AllDrivers/STEP6: U4.15 (LED8); also elsewhere on the board
/FAN_PWM: U4.22 (LED15); also elsewhere on the board
/I2C_SCL: R1.2, U4.26 (SCL); also elsewhere on the board
/I2C_SDA: R2.2, U4.27 (SDA); also elsewhere on the board
GND: C1.2, C2.2, C3.2, C4.2, C5.2, C6.2, C7.2, CR1.1 (ADJ/GND), D2.2 (A), U1.2 (GND), U3.3 (GND), U3.5 (~ON), U4.1 (A0), U4.2 (A1), U4.3 (A2), U4.4 (A3), U4.5 (A4), U4.14 (VSS), U4.25 (EXTCLK); also elsewhere on the board
unnamed: D2.1 (K), L2.1, U3.2 (OUTPUT)
unnamed: R3.2, U4.23 (~OE)
VCC: C6.1, CR1.3 (VOUT), R1.1, R2.1, R3.1, U4.24 (A5), U4.28 (VDD); also elsewhere on the board

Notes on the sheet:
BATT to 12V conv
12V to 5V
BATT to 3.3V conv

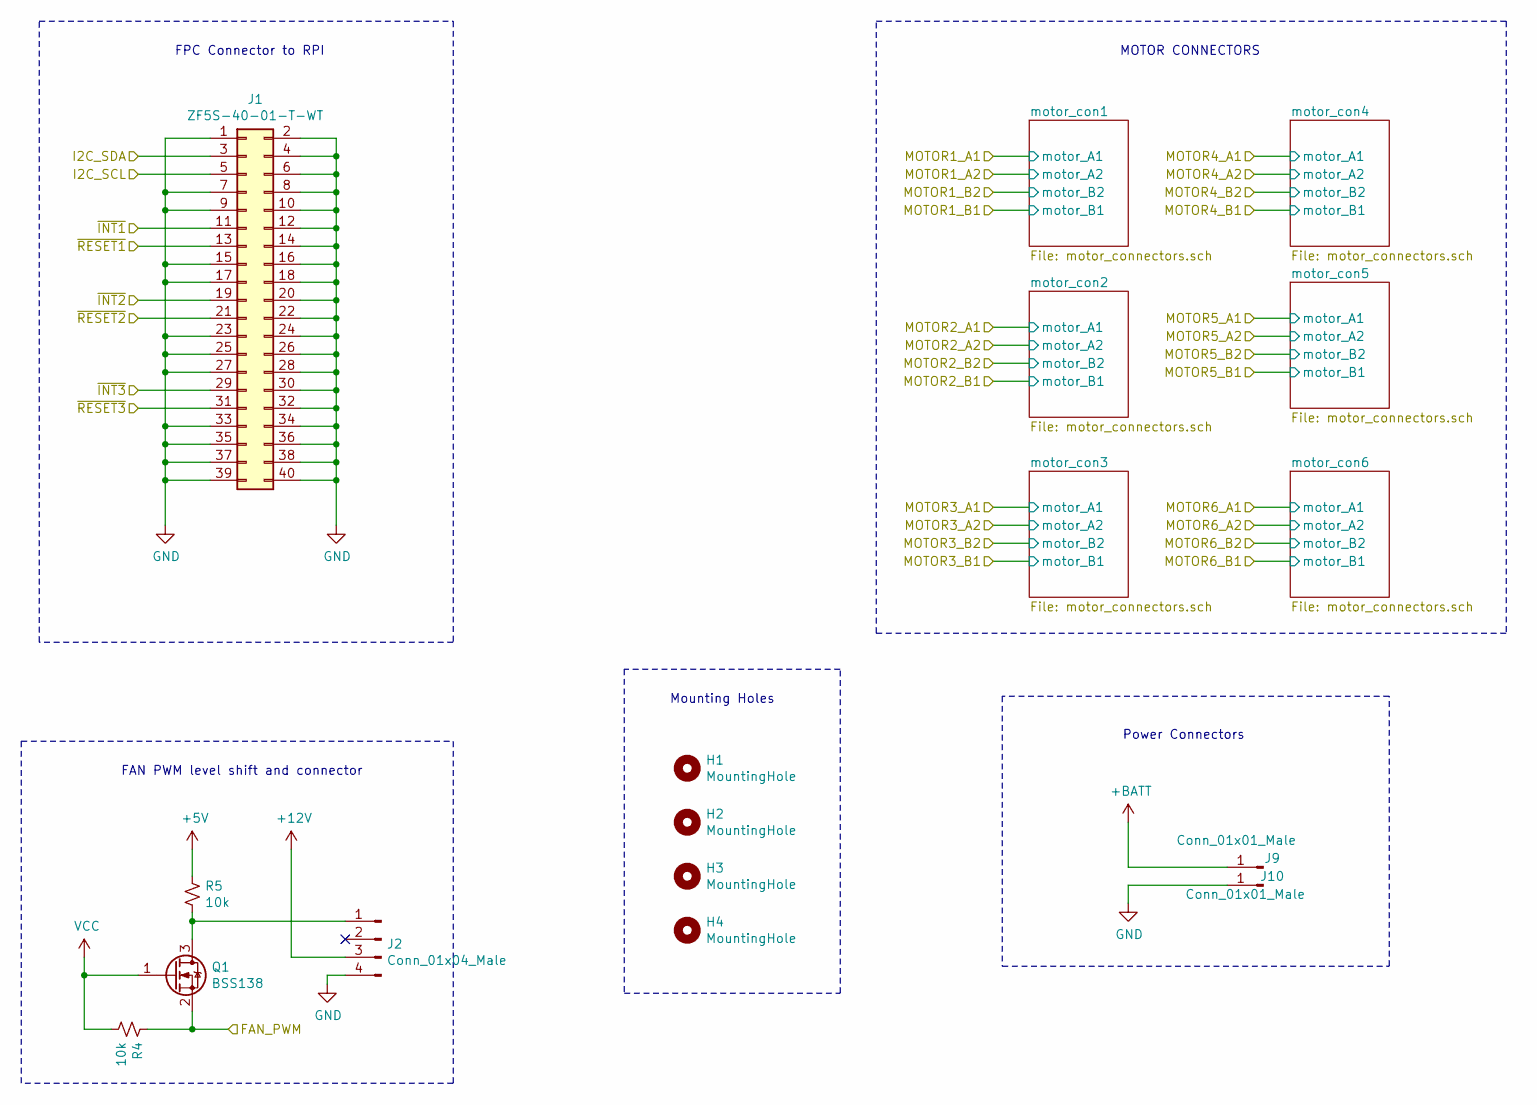
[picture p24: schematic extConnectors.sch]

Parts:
H1, H2, H3, H4: MountingHole; MountingHole_3.2mm_M3_ISO14580
J1: ZF5S-40-01-T-WT; FPC_40
J2: Conn_01x04_Male; FanPinHeader_1x04_P2.54mm_Vertical
J9, J10: Conn_01x01_Male; TestPoint_Pad_4.0x4.0mm
Q1: BSS138; SOT-23
R4, R5: 10k; R_0603_1608Metric_Pad0.98x0.95mm_HandSolder

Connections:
+5V: R5.1; also elsewhere on the board
+12V: J2.3; also elsewhere on the board
+BATT: J9.1; also elsewhere on the board
/AllDrivers/~INT1: J1.11; also elsewhere on the board
/AllDrivers/~INT2: J1.19; also elsewhere on the board
/AllDrivers/~INT3: J1.29; also elsewhere on the board
/AllDrivers/~RESET1: J1.13; also elsewhere on the board
/AllDrivers/~RESET2: J1.21; also elsewhere on the board
/AllDrivers/~RESET3: J1.31; also elsewhere on the board
/FAN_PWM: Q1.2 (S), R4.1; also elsewhere on the board
/I2C_SCL: J1.5; also elsewhere on the board
/I2C_SDA: J1.3; also elsewhere on the board
GND: J1.1, J1.2, J1.4, J1.6, J1.7, J1.8, J1.9, J1.10, J1.12, J1.14, J1.15, J1.16, J1.17, J1.18, J1.20, J1.22, J1.23, J1.24, J1.25, J1.26, J1.27, J1.28, J1.30, J1.32, J1.33, J1.34, J1.35, J1.36, J1.37, J1.38, J1.39, J1.40, J2.4, J10.1; also elsewhere on the board
unnamed: J2.1, Q1.3 (D), R5.2
VCC: Q1.1 (G), R4.2; also elsewhere on the board

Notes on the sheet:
MOTOR CONNECTORS
FPC Connector to RPI
FAN PWM level shift and connector
Power Connectors
Mounting Holes

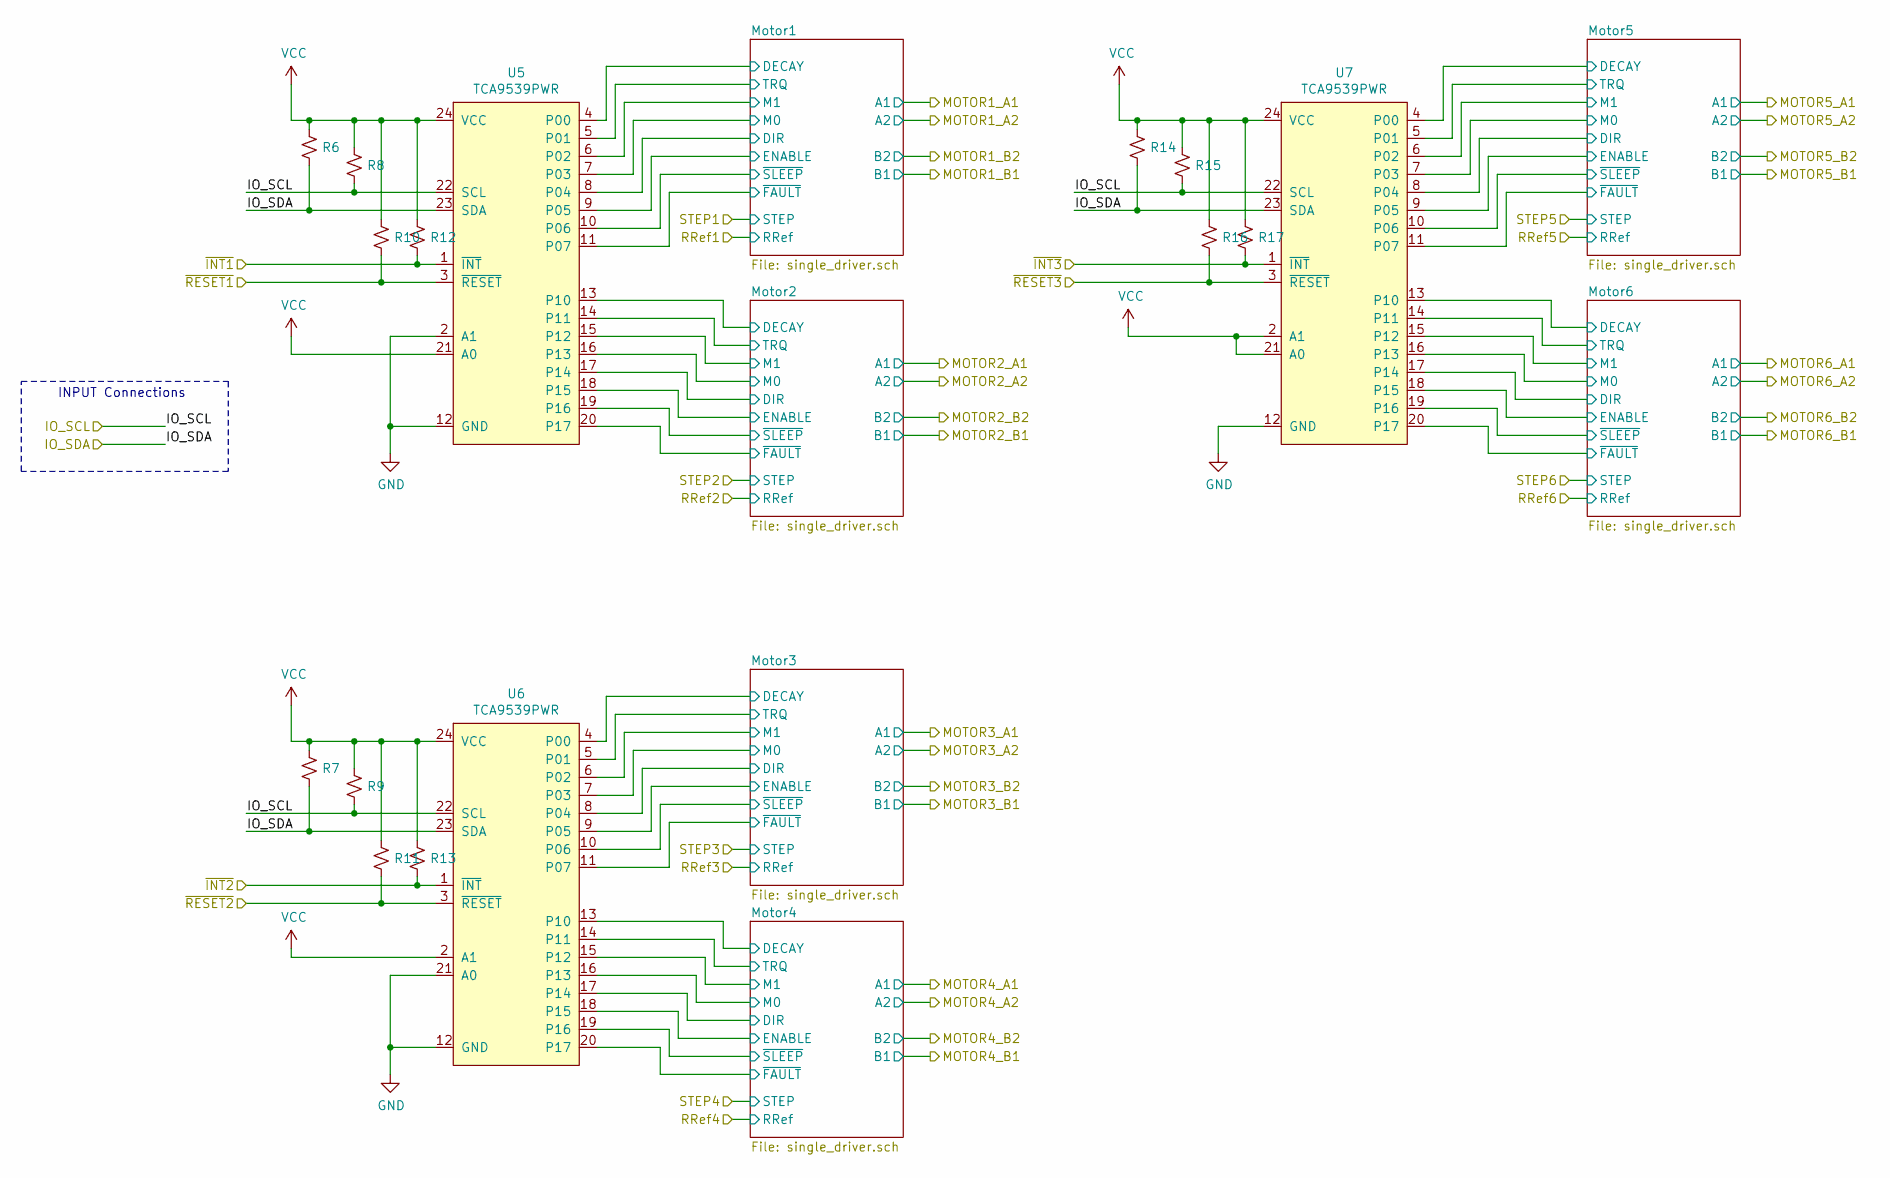
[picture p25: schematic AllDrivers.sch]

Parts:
R6, R7, R8, R9, R10, R11, R12, R13, R14, R15, R16, R17: 1; R_0603_1608Metric_Pad0.98x0.95mm_HandSolder
U5, U6, U7: TCA9539PWR; TCA9539_TSSOP-24

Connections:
/AllDrivers/Motor1/DECAY: U5.4 (P00); also elsewhere on the board
/AllDrivers/Motor1/DIR: U5.8 (P04); also elsewhere on the board
/AllDrivers/Motor1/ENABLE: U5.9 (P05); also elsewhere on the board
/AllDrivers/Motor1/M0: U5.7 (P03); also elsewhere on the board
/AllDrivers/Motor1/M1: U5.6 (P02); also elsewhere on the board
/AllDrivers/Motor1/TRQ: U5.5 (P01); also elsewhere on the board
/AllDrivers/Motor1/~FAULT: U5.11 (P07); also elsewhere on the board
/AllDrivers/Motor1/~SLEEP: U5.10 (P06); also elsewhere on the board
/AllDrivers/Motor2/DECAY: U5.13 (P10); also elsewhere on the board
/AllDrivers/Motor2/DIR: U5.17 (P14); also elsewhere on the board
/AllDrivers/Motor2/ENABLE: U5.18 (P15); also elsewhere on the board
/AllDrivers/Motor2/M0: U5.16 (P13); also elsewhere on the board
/AllDrivers/Motor2/M1: U5.15 (P12); also elsewhere on the board
/AllDrivers/Motor2/TRQ: U5.14 (P11); also elsewhere on the board
/AllDrivers/Motor2/~FAULT: U5.20 (P17); also elsewhere on the board
/AllDrivers/Motor2/~SLEEP: U5.19 (P16); also elsewhere on the board
/AllDrivers/Motor3/DECAY: U6.4 (P00); also elsewhere on the board
/AllDrivers/Motor3/DIR: U6.8 (P04); also elsewhere on the board
/AllDrivers/Motor3/ENABLE: U6.9 (P05); also elsewhere on the board
/AllDrivers/Motor3/M0: U6.7 (P03); also elsewhere on the board
/AllDrivers/Motor3/M1: U6.6 (P02); also elsewhere on the board
/AllDrivers/Motor3/TRQ: U6.5 (P01); also elsewhere on the board
/AllDrivers/Motor3/~FAULT: U6.11 (P07); also elsewhere on the board
/AllDrivers/Motor3/~SLEEP: U6.10 (P06); also elsewhere on the board
/AllDrivers/Motor4/DECAY: U6.13 (P10); also elsewhere on the board
/AllDrivers/Motor4/DIR: U6.17 (P14); also elsewhere on the board
/AllDrivers/Motor4/ENABLE: U6.18 (P15); also elsewhere on the board
/AllDrivers/Motor4/M0: U6.16 (P13); also elsewhere on the board
/AllDrivers/Motor4/M1: U6.15 (P12); also elsewhere on the board
/AllDrivers/Motor4/TRQ: U6.14 (P11); also elsewhere on the board
/AllDrivers/Motor4/~FAULT: U6.20 (P17); also elsewhere on the board
/AllDrivers/Motor4/~SLEEP: U6.19 (P16); also elsewhere on the board
/AllDrivers/Motor5/DECAY: U7.4 (P00); also elsewhere on the board
/AllDrivers/Motor5/DIR: U7.8 (P04); also elsewhere on the board
/AllDrivers/Motor5/ENABLE: U7.9 (P05); also elsewhere on the board
/AllDrivers/Motor5/M0: U7.7 (P03); also elsewhere on the board
/AllDrivers/Motor5/M1: U7.6 (P02); also elsewhere on the board
/AllDrivers/Motor5/TRQ: U7.5 (P01); also elsewhere on the board
/AllDrivers/Motor5/~FAULT: U7.11 (P07); also elsewhere on the board
/AllDrivers/Motor5/~SLEEP: U7.10 (P06); also elsewhere on the board
/AllDrivers/Motor6/DECAY: U7.13 (P10); also elsewhere on the board
/AllDrivers/Motor6/DIR: U7.17 (P14); also elsewhere on the board
/AllDrivers/Motor6/ENABLE: U7.18 (P15); also elsewhere on the board
/AllDrivers/Motor6/M0: U7.16 (P13); also elsewhere on the board
/AllDrivers/Motor6/M1: U7.15 (P12); also elsewhere on the board
/AllDrivers/Motor6/TRQ: U7.14 (P11); also elsewhere on the board
/AllDrivers/Motor6/~FAULT: U7.20 (P17); also elsewhere on the board
/AllDrivers/Motor6/~SLEEP: U7.19 (P16); also elsewhere on the board
/AllDrivers/~INT1: R12.2, U5.1 (~INT); also elsewhere on the board
/AllDrivers/~INT2: R13.2, U6.1 (~INT); also elsewhere on the board
/AllDrivers/~INT3: R17.2, U7.1 (~INT); also elsewhere on the board
/AllDrivers/~RESET1: R10.2, U5.3 (~RESET); also elsewhere on the board
/AllDrivers/~RESET2: R11.2, U6.3 (~RESET); also elsewhere on the board
/AllDrivers/~RESET3: R16.2, U7.3 (~RESET); also elsewhere on the board
/I2C_SCL: R8.2, R9.2, R15.2, U5.22 (SCL), U6.22 (SCL), U7.22 (SCL); also elsewhere on the board
/I2C_SDA: R6.2, R7.2, R14.2, U5.23 (SDA), U6.23 (SDA), U7.23 (SDA); also elsewhere on the board
GND: U5.2 (A1), U5.12 (GND), U6.12 (GND), U6.21 (A0), U7.12 (GND); also elsewhere on the board
VCC: R6.1, R7.1, R8.1, R9.1, R10.1, R11.1, R12.1, R13.1, R14.1, R15.1, R16.1, R17.1, U5.21 (A0), U5.24 (VCC), U6.2 (A1), U6.24 (VCC), U7.2 (A1), U7.21 (A0), U7.24 (VCC); also elsewhere on the board

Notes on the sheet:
INPUT Connections

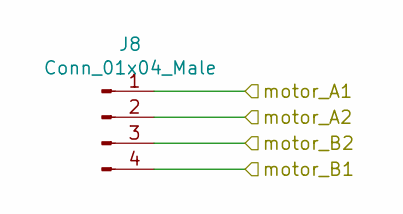
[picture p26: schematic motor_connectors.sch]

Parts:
J3: Conn_01x04_Male; PhoenixContact_MSTBVA_2,5_4-G-5,08_1x04_P5.08mm_Vertical

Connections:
/AllDrivers/MOTOR1_A1: J3.1; also elsewhere on the board
/AllDrivers/MOTOR1_A2: J3.2; also elsewhere on the board
/AllDrivers/MOTOR1_B1: J3.4; also elsewhere on the board
/AllDrivers/MOTOR1_B2: J3.3; also elsewhere on the board

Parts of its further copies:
J4, J5, J6, J7, J8: Conn_01x04_Male; PhoenixContact_MSTBVA_2,5_4-G-5,08_1x04_P5.08mm_Vertical

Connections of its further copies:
/AllDrivers/MOTOR2_A1: J4.1; also elsewhere on the board
/AllDrivers/MOTOR2_A2: J4.2; also elsewhere on the board
/AllDrivers/MOTOR2_B1: J4.4; also elsewhere on the board
/AllDrivers/MOTOR2_B2: J4.3; also elsewhere on the board
/AllDrivers/MOTOR3_A1: J5.1; also elsewhere on the board
/AllDrivers/MOTOR3_A2: J5.2; also elsewhere on the board
/AllDrivers/MOTOR3_B1: J5.4; also elsewhere on the board
/AllDrivers/MOTOR3_B2: J5.3; also elsewhere on the board
/AllDrivers/MOTOR4_A1: J6.1; also elsewhere on the board
/AllDrivers/MOTOR4_A2: J6.2; also elsewhere on the board
/AllDrivers/MOTOR4_B1: J6.4; also elsewhere on the board
/AllDrivers/MOTOR4_B2: J6.3; also elsewhere on the board
/AllDrivers/MOTOR5_A1: J7.1; also elsewhere on the board
/AllDrivers/MOTOR5_A2: J7.2; also elsewhere on the board
/AllDrivers/MOTOR5_B1: J7.4; also elsewhere on the board
/AllDrivers/MOTOR5_B2: J7.3; also elsewhere on the board
/AllDrivers/MOTOR6_A1: J8.1; also elsewhere on the board
/AllDrivers/MOTOR6_A2: J8.2; also elsewhere on the board
/AllDrivers/MOTOR6_B1: J8.4; also elsewhere on the board
/AllDrivers/MOTOR6_B2: J8.3; also elsewhere on the board

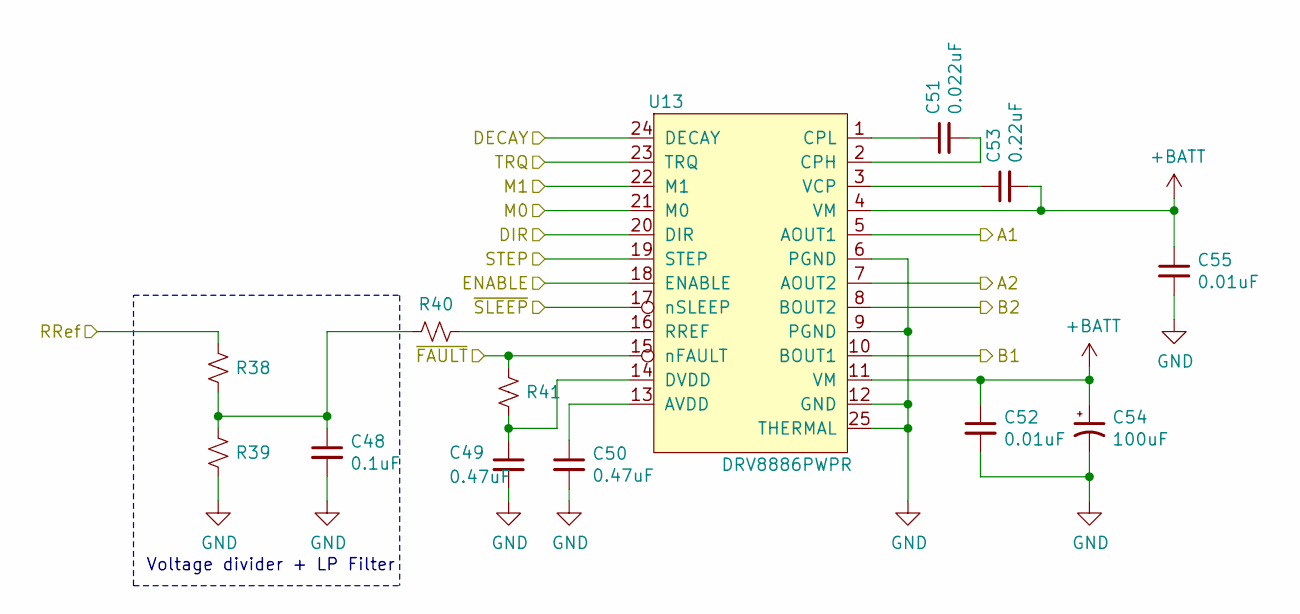
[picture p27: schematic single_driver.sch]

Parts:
C8: 0.1uF; C_0603_1608Metric_Pad1.08x0.95mm_HandSolder
C9, C10: 0.47uF; C_0805_2012Metric_Pad1.18x1.45mm_HandSolder
C11: 0.022uF; C_0603_1608Metric_Pad1.08x0.95mm_HandSolder
C12, C15: 0.01uF; C_0603_1608Metric_Pad1.08x0.95mm_HandSolder
C13: 0.22uF; C_0603_1608Metric_Pad1.08x0.95mm_HandSolder
C14: 100uF; CP_Elec_8x6.2
R18, R19, R21: R_Small_US; R_0603_1608Metric_Pad0.98x0.95mm_HandSolder
R20: rref; R_0603_1608Metric_Pad0.98x0.95mm_HandSolder
U8: DRV8886PWPR‎; DRV8886_HTSSOP-24

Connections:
+BATT: C12.1, C13.2, C14.1, C15.1, U8.4 (VM), U8.11 (VM); also elsewhere on the board
/AllDrivers/MOTOR4_A1: U8.5 (AOUT1); also elsewhere on the board
/AllDrivers/MOTOR4_A2: U8.7 (AOUT2); also elsewhere on the board
/AllDrivers/MOTOR4_B1: U8.10 (BOUT1); also elsewhere on the board
/AllDrivers/MOTOR4_B2: U8.8 (BOUT2); also elsewhere on the board
/AllDrivers/Motor4/DECAY: U8.24 (DECAY); also elsewhere on the board
/AllDrivers/Motor4/DIR: U8.20 (DIR); also elsewhere on the board
/AllDrivers/Motor4/ENABLE: U8.18 (ENABLE); also elsewhere on the board
/AllDrivers/Motor4/M0: U8.21 (M0); also elsewhere on the board
/AllDrivers/Motor4/M1: U8.22 (M1); also elsewhere on the board
/AllDrivers/Motor4/TRQ: U8.23 (TRQ); also elsewhere on the board
/AllDrivers/Motor4/~FAULT: R21.1, U8.15 (nFAULT); also elsewhere on the board
/AllDrivers/Motor4/~SLEEP: U8.17 (nSLEEP); also elsewhere on the board
/AllDrivers/RRef4: R18.1; also elsewhere on the board
/AllDrivers/STEP4: U8.19 (STEP); also elsewhere on the board
GND: C8.2, C9.2, C10.2, C12.2, C14.2, C15.2, R19.2, U8.6 (PGND), U8.9 (PGND), U8.12 (GND), U8.25 (THERMAL); also elsewhere on the board
unnamed: C8.1, R18.2, R19.1, R20.1
unnamed: C9.1, R21.2, U8.14 (DVDD)
unnamed: C10.1, U8.13 (AVDD)
unnamed: C11.1, U8.1 (CPL)
unnamed: C11.2, U8.2 (CPH)
unnamed: C13.1, U8.3 (VCP)
unnamed: R20.2, U8.16 (RREF)

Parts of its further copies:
C16, C24, C32, C40, C48: 0.1uF; C_0603_1608Metric_Pad1.08x0.95mm_HandSolder
C17, C18, C25, C26, C33, C34, C41, C42, C49, C50: 0.47uF; C_0805_2012Metric_Pad1.18x1.45mm_HandSolder
C19, C27, C35, C43, C51: 0.022uF; C_0603_1608Metric_Pad1.08x0.95mm_HandSolder
C20, C23, C28, C31, C36, C39, C44, C47, C52, C55: 0.01uF; C_0603_1608Metric_Pad1.08x0.95mm_HandSolder
C21, C29, C37, C45, C53: 0.22uF; C_0603_1608Metric_Pad1.08x0.95mm_HandSolder
C22, C30, C38, C46, C54: 100uF; CP_Elec_8x6.2
R22, R23, R25, R26, R27, R29, R30, R31, R33, R34, R35, R37, R38, R39, R41: R_Small_US; R_0603_1608Metric_Pad0.98x0.95mm_HandSolder
R24, R28, R32, R36, R40: rref; R_0603_1608Metric_Pad0.98x0.95mm_HandSolder
U9, U10, U11, U12, U13: DRV8886PWPR‎; DRV8886_HTSSOP-24

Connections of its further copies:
+BATT: C20.1, C21.2, C22.1, C23.1, C28.1, C29.2, C30.1, C31.1, C36.1, C37.2, C38.1, C39.1, C44.1, C45.2, C46.1, C47.1, C52.1, C53.2, C54.1, C55.1, U9.4 (VM), U9.11 (VM), U10.4 (VM), U10.11 (VM), U11.4 (VM), U11.11 (VM), U12.4 (VM), U12.11 (VM), U13.4 (VM), U13.11 (VM); also elsewhere on the board
/AllDrivers/MOTOR1_A1: U11.5 (AOUT1); also elsewhere on the board
/AllDrivers/MOTOR1_A2: U11.7 (AOUT2); also elsewhere on the board
/AllDrivers/MOTOR1_B1: U11.10 (BOUT1); also elsewhere on the board
/AllDrivers/MOTOR1_B2: U11.8 (BOUT2); also elsewhere on the board
/AllDrivers/MOTOR2_A1: U10.5 (AOUT1); also elsewhere on the board
/AllDrivers/MOTOR2_A2: U10.7 (AOUT2); also elsewhere on the board
/AllDrivers/MOTOR2_B1: U10.10 (BOUT1); also elsewhere on the board
/AllDrivers/MOTOR2_B2: U10.8 (BOUT2); also elsewhere on the board
/AllDrivers/MOTOR3_A1: U9.5 (AOUT1); also elsewhere on the board
/AllDrivers/MOTOR3_A2: U9.7 (AOUT2); also elsewhere on the board
/AllDrivers/MOTOR3_B1: U9.10 (BOUT1); also elsewhere on the board
/AllDrivers/MOTOR3_B2: U9.8 (BOUT2); also elsewhere on the board
/AllDrivers/MOTOR5_A1: U12.5 (AOUT1); also elsewhere on the board
/AllDrivers/MOTOR5_A2: U12.7 (AOUT2); also elsewhere on the board
/AllDrivers/MOTOR5_B1: U12.10 (BOUT1); also elsewhere on the board
/AllDrivers/MOTOR5_B2: U12.8 (BOUT2); also elsewhere on the board
/AllDrivers/MOTOR6_A1: U13.5 (AOUT1); also elsewhere on the board
/AllDrivers/MOTOR6_A2: U13.7 (AOUT2); also elsewhere on the board
/AllDrivers/MOTOR6_B1: U13.10 (BOUT1); also elsewhere on the board
/AllDrivers/MOTOR6_B2: U13.8 (BOUT2); also elsewhere on the board
/AllDrivers/Motor1/DECAY: U11.24 (DECAY); also elsewhere on the board
/AllDrivers/Motor1/DIR: U11.20 (DIR); also elsewhere on the board
/AllDrivers/Motor1/ENABLE: U11.18 (ENABLE); also elsewhere on the board
/AllDrivers/Motor1/M0: U11.21 (M0); also elsewhere on the board
/AllDrivers/Motor1/M1: U11.22 (M1); also elsewhere on the board
/AllDrivers/Motor1/TRQ: U11.23 (TRQ); also elsewhere on the board
/AllDrivers/Motor1/~FAULT: R33.1, U11.15 (nFAULT); also elsewhere on the board
/AllDrivers/Motor1/~SLEEP: U11.17 (nSLEEP); also elsewhere on the board
/AllDrivers/Motor2/DECAY: U10.24 (DECAY); also elsewhere on the board
/AllDrivers/Motor2/DIR: U10.20 (DIR); also elsewhere on the board
/AllDrivers/Motor2/ENABLE: U10.18 (ENABLE); also elsewhere on the board
/AllDrivers/Motor2/M0: U10.21 (M0); also elsewhere on the board
/AllDrivers/Motor2/M1: U10.22 (M1); also elsewhere on the board
/AllDrivers/Motor2/TRQ: U10.23 (TRQ); also elsewhere on the board
/AllDrivers/Motor2/~FAULT: R29.1, U10.15 (nFAULT); also elsewhere on the board
/AllDrivers/Motor2/~SLEEP: U10.17 (nSLEEP); also elsewhere on the board
/AllDrivers/Motor3/DECAY: U9.24 (DECAY); also elsewhere on the board
/AllDrivers/Motor3/DIR: U9.20 (DIR); also elsewhere on the board
/AllDrivers/Motor3/ENABLE: U9.18 (ENABLE); also elsewhere on the board
/AllDrivers/Motor3/M0: U9.21 (M0); also elsewhere on the board
/AllDrivers/Motor3/M1: U9.22 (M1); also elsewhere on the board
/AllDrivers/Motor3/TRQ: U9.23 (TRQ); also elsewhere on the board
/AllDrivers/Motor3/~FAULT: R25.1, U9.15 (nFAULT); also elsewhere on the board
/AllDrivers/Motor3/~SLEEP: U9.17 (nSLEEP); also elsewhere on the board
/AllDrivers/Motor5/DECAY: U12.24 (DECAY); also elsewhere on the board
/AllDrivers/Motor5/DIR: U12.20 (DIR); also elsewhere on the board
/AllDrivers/Motor5/ENABLE: U12.18 (ENABLE); also elsewhere on the board
/AllDrivers/Motor5/M0: U12.21 (M0); also elsewhere on the board
/AllDrivers/Motor5/M1: U12.22 (M1); also elsewhere on the board
/AllDrivers/Motor5/TRQ: U12.23 (TRQ); also elsewhere on the board
/AllDrivers/Motor5/~FAULT: R37.1, U12.15 (nFAULT); also elsewhere on the board
/AllDrivers/Motor5/~SLEEP: U12.17 (nSLEEP); also elsewhere on the board
/AllDrivers/Motor6/DECAY: U13.24 (DECAY); also elsewhere on the board
/AllDrivers/Motor6/DIR: U13.20 (DIR); also elsewhere on the board
/AllDrivers/Motor6/ENABLE: U13.18 (ENABLE); also elsewhere on the board
/AllDrivers/Motor6/M0: U13.21 (M0); also elsewhere on the board
/AllDrivers/Motor6/M1: U13.22 (M1); also elsewhere on the board
/AllDrivers/Motor6/TRQ: U13.23 (TRQ); also elsewhere on the board
/AllDrivers/Motor6/~FAULT: R41.1, U13.15 (nFAULT); also elsewhere on the board
/AllDrivers/Motor6/~SLEEP: U13.17 (nSLEEP); also elsewhere on the board
/AllDrivers/RRef1: R30.1; also elsewhere on the board
/AllDrivers/RRef2: R26.1; also elsewhere on the board
/AllDrivers/RRef3: R22.1; also elsewhere on the board
/AllDrivers/RRef5: R34.1; also elsewhere on the board
/AllDrivers/RRef6: R38.1; also elsewhere on the board
/AllDrivers/STEP1: U11.19 (STEP); also elsewhere on the board
/AllDrivers/STEP2: U10.19 (STEP); also elsewhere on the board
/AllDrivers/STEP3: U9.19 (STEP); also elsewhere on the board
/AllDrivers/STEP5: U12.19 (STEP); also elsewhere on the board
/AllDrivers/STEP6: U13.19 (STEP); also elsewhere on the board
GND: C16.2, C17.2, C18.2, C20.2, C22.2, C23.2, C24.2, C25.2, C26.2, C28.2, C30.2, C31.2, C32.2, C33.2, C34.2, C36.2, C38.2, C39.2, C40.2, C41.2, C42.2, C44.2, C46.2, C47.2, C48.2, C49.2, C50.2, C52.2, C54.2, C55.2, R23.2, R27.2, R31.2, R35.2, R39.2, U9.6 (PGND), U9.9 (PGND), U9.12 (GND), U9.25 (THERMAL), U10.6 (PGND), U10.9 (PGND), U10.12 (GND), U10.25 (THERMAL), U11.6 (PGND), U11.9 (PGND), U11.12 (GND), U11.25 (THERMAL), U12.6 (PGND), U12.9 (PGND), U12.12 (GND), U12.25 (THERMAL), U13.6 (PGND), U13.9 (PGND), U13.12 (GND), U13.25 (THERMAL); also elsewhere on the board
unnamed: C16.1, R22.2, R23.1, R24.1
unnamed: C17.1, R25.2, U9.14 (DVDD)
unnamed: C18.1, U9.13 (AVDD)
unnamed: C19.1, U9.1 (CPL)
unnamed: C19.2, U9.2 (CPH)
unnamed: C21.1, U9.3 (VCP)
unnamed: C24.1, R26.2, R27.1, R28.1
unnamed: C25.1, R29.2, U10.14 (DVDD)
unnamed: C26.1, U10.13 (AVDD)
unnamed: C27.1, U10.1 (CPL)
unnamed: C27.2, U10.2 (CPH)
unnamed: C29.1, U10.3 (VCP)
unnamed: C32.1, R30.2, R31.1, R32.1
unnamed: C33.1, R33.2, U11.14 (DVDD)
unnamed: C34.1, U11.13 (AVDD)
unnamed: C35.1, U11.1 (CPL)
unnamed: C35.2, U11.2 (CPH)
unnamed: C37.1, U11.3 (VCP)
unnamed: C40.1, R34.2, R35.1, R36.1
unnamed: C41.1, R37.2, U12.14 (DVDD)
unnamed: C42.1, U12.13 (AVDD)
unnamed: C43.1, U12.1 (CPL)
unnamed: C43.2, U12.2 (CPH)
unnamed: C45.1, U12.3 (VCP)
unnamed: C48.1, R38.2, R39.1, R40.1
unnamed: C49.1, R41.2, U13.14 (DVDD)
unnamed: C50.1, U13.13 (AVDD)
unnamed: C51.1, U13.1 (CPL)
unnamed: C51.2, U13.2 (CPH)
unnamed: C53.1, U13.3 (VCP)
unnamed: R24.2, U9.16 (RREF)
unnamed: R28.2, U10.16 (RREF)
unnamed: R32.2, U11.16 (RREF)
unnamed: R36.2, U12.16 (RREF)
unnamed: R40.2, U13.16 (RREF)

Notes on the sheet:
Voltage divider + LP Filter

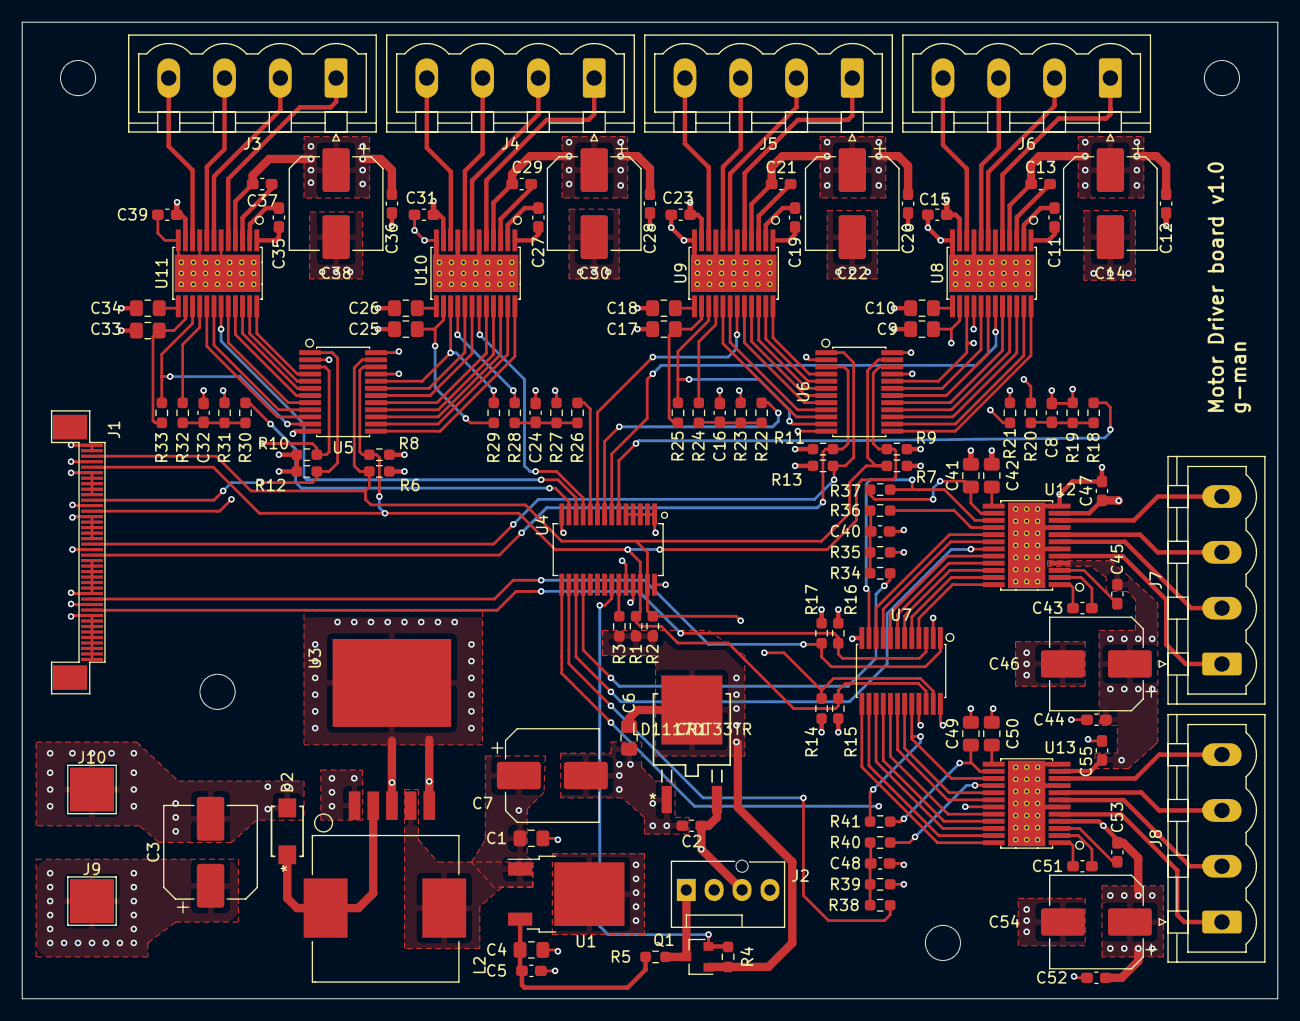
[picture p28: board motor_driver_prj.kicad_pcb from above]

Board: 4 copper layers, 114.3 x 88.9 mm, 126 parts (0 on the bottom side), 143 nets.

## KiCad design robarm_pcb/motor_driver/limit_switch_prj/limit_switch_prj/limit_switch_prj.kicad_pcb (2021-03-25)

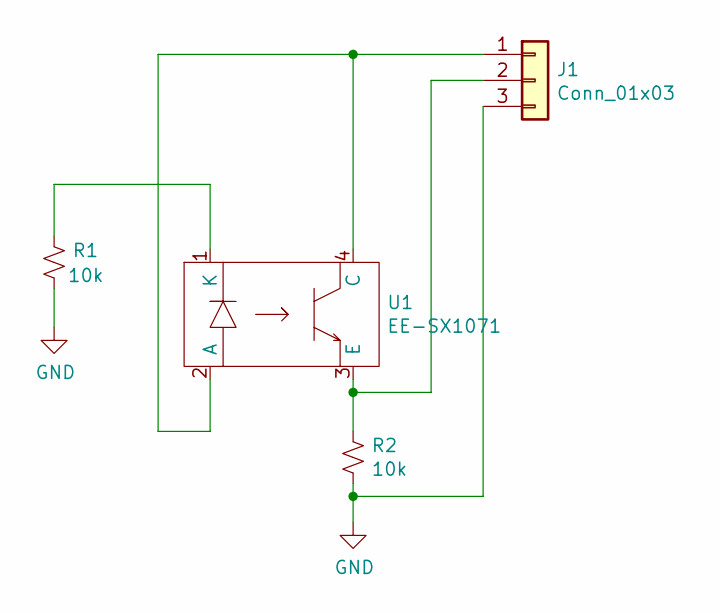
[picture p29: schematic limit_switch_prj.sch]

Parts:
J1: Conn_01x03; picoblade-conn-1.25mm-3pin
R1, R2: 10k; R_0603_1608Metric_Pad0.98x0.95mm_HandSolder
U1: EE-SX1071

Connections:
GND: J1.3, R1.2, R2.2
unnamed: J1.1, U1.2 (A), U1.4 (C)
unnamed: J1.2, R2.1, U1.3 (E)
unnamed: R1.1, U1.1 (K)

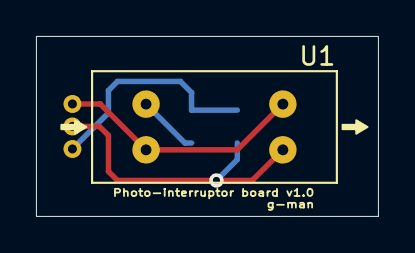
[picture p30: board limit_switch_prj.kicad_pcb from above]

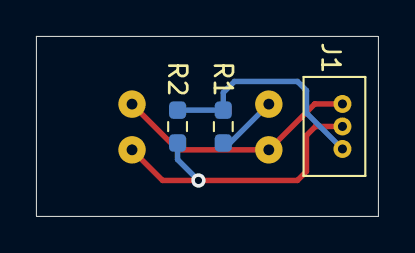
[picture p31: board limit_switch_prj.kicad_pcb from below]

Board: 2 copper layers, 19.0 x 10.0 mm, 4 parts (3 on the bottom side), 4 nets.

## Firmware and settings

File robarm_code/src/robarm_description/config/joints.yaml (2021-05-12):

robarm:
  # Publish all joint states -----------------------------------
  joint_state_controller:
    type: joint_state_controller/JointStateController
    publish_rate: 50  
  
  # Position Controllers ---------------------------------------
  joint1_position_controller:
    type: effort_controllers/JointPositionController
    joint: joint1
    pid: {p: 100.0, i: 0.01, d: 10.0}
  joint2_position_controller:
    type: effort_controllers/JointPositionController
    joint: joint2
    pid: {p: 100.0, i: 0.01, d: 10.0}
  joint3_position_controller:
    type: effort_controllers/JointPositionController
    joint: joint3
    pid: {p: 100.0, i: 0.01, d: 10.0}

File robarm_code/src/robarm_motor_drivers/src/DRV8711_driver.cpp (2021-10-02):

/**
 * @file DRV8711_driver.cpp
 * @author your name (you@domain.com)
 * @brief 
 * @version 0.1
 * @date 2021-09-08
 * 
 * @copyright Copyright (c) 2021
 * 
 */



#include "DRV8711_driver.h"

using namespace std;


/**
 * @brief Construct a new drv8711 driver::drv8711 driver object
 * 
 * @param spiChannel 
 * @param spiBaudRate 
 */
DRV8711_driver::DRV8711_driver(__u32 spiChannel, __u8 spiMode, __u32 spiBaudRate, __u8 spiBitsPerWord) {
  
  ErrorCodes_Type errCode;

  this->_spiChannel = spiChannel;
  this->_spiMode = spiMode;
  this->_spiBaudRate = spiBaudRate;
  this->_spiBitsPerWord = spiBitsPerWord;

  errCode = _SPI_init();

  cout << "spi init result: " << errCode << endl;

}

/**
 * @brief Destroy the drv8711 driver::drv8711 driver object
 * 
 */
DRV8711_driver::~DRV8711_driver() {

  close(this->_spiFd);

}

/**
 * @brief Initialize the SPI driver
 * 
 * @param spiChannel 
 * @param spiBaudRate 
 * @return ErrorCodes_Type 
 */
auto DRV8711_driver::_SPI_init() -> ErrorCodes_Type {
    
  ErrorCodes_Type errCode = _NO_ERROR;
  char dev[32];
  int err;

  sprintf(dev, "/dev/spidev0.%d", this->_spiChannel);
  this->_spiFd = open(dev, O_RDWR);

  if (this->_spiFd < 0)
  {
    errCode = _SPI_INIT_FAIL_OPENDEV;
    return errCode;
  }

  if (ioctl(this->_spiFd, SPI_IOC_WR_MODE, &this->_spiMode) < 0)
  {
    errCode = _SPI_INIT_FAIL_MODE;
    cout << "err: " << err << endl;
    cout << "error in setting mode: " << strerror(errno) << endl;
    close(this->_spiFd);
    return errCode;    
  }

  if (ioctl(this->_spiFd, SPI_IOC_WR_BITS_PER_WORD, &this->_spiBitsPerWord) < 0)
  {
    close(this->_spiFd);
    cout << "error in setting mode: " << strerror(errno) << endl;
    errCode = _SPI_INIT_FAIL_BITS_PER_WORD;
    return errCode;
  }

  if (ioctl(this->_spiFd, SPI_IOC_WR_MAX_SPEED_HZ, &this->_spiBaudRate) < 0)
  {
    close(this->_spiFd);
    errCode = _SPI_INIT_FAIL_BAUD_RATE;
    return errCode;
  }

  return errCode;

}

/**
 * @brief 
 * 
 * @param rxBuf 
 * @param rxBufCount 
 * @return ErrorCodes_Type 
 */
auto DRV8711_driver::_SPI_read(__u8 *rxBuf, __u32 rxBufCount) -> ErrorCodes_Type{

  ErrorCodes_Type errCode;
  struct spi_ioc_transfer spi;

  int err;
  
  memset(&spi, 0, sizeof(spi));

  spi.tx_buf        = (unsigned long)NULL;
  spi.rx_buf        = (unsigned long)rxBuf;
  spi.len           = rxBufCount;
  spi.speed_hz      = _CONFIG_SPI_BAUD_RATE;
  spi.delay_usecs   = 0;
  spi.bits_per_word = 8;
  spi.cs_change     = 0;

  err = ioctl(this->_spiFd, SPI_IOC_MESSAGE(1), &spi);
  errCode = (err == 0) ? _NO_ERROR : _SPI_READ_FAIL;

  return errCode;
}

/**
 * @brief 
 * 
 * @param txBuf 
 * @param txBufCount 
 * @return ErrorCodes_Type 
 */
auto DRV8711_driver::_SPI_write(__u8 *txBuf, __u32 txBufCount) -> ErrorCodes_Type{

  ErrorCodes_Type errCode;
  struct spi_ioc_transfer spi;

  int err;
  
  memset(&spi, 0, sizeof(spi));

  spi.tx_buf        = (unsigned long)txBuf;
  spi.rx_buf        = (unsigned long)NULL;
  spi.len           = txBufCount;
  spi.speed_hz      = _CONFIG_SPI_BAUD_RATE;
  spi.delay_usecs   = 0;
  spi.bits_per_word = 8;
  spi.cs_change     = 0;

  err = ioctl(this->_spiFd, SPI_IOC_MESSAGE(1), &spi);
  errCode = (err == 0) ? _NO_ERROR : _SPI_WRITE_FAIL;

  return errCode;
}

/**
 * @brief 
 * 
 * @param rxBuf 
 * @param txBuf 
 * @param bufCount 
 * @return ErrorCodes_Type 
 */
auto DRV8711_driver::_SPI_transfer(__u8 *rxBuf, __u8 *txBuf, __u32 bufCount) -> ErrorCodes_Type{

  ErrorCodes_Type errCode;
  struct spi_ioc_transfer spi;

  int err;
  
  memset(&spi, 0, sizeof(spi));

  spi.tx_buf        = (unsigned long)txBuf;
  spi.rx_buf        = (unsigned long)rxBuf;
  spi.len           = bufCount;
  spi.speed_hz      = _CONFIG_SPI_BAUD_RATE;
  spi.delay_usecs   = 0;
  spi.bits_per_word = 8;
  spi.cs_change     = 0;

  err = ioctl(this->_spiFd, SPI_IOC_MESSAGE(1), &spi);
  errCode = (err == 0) ? _NO_ERROR : _SPI_TRANSFER_FAIL;

  return errCode;
}

/**
 * @brief 
 * 
 * @param speed 
 * @return ErrorCodes_Type 
 */
auto DRV8711_driver::setSpeed(__u8 speed) -> ErrorCodes_Type {

  ErrorCodes_Type err;

  err = _SPI_write(&speed, 1);
  
  return err;

}

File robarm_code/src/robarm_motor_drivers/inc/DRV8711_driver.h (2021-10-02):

/**
 * @file DRV8711_driver.h
 * @author Gaurav Manda (grvmanda@gmail.com)
 * @brief 
 * @version 0.1
 * @date 2021-09-08
 * 
 * @copyright Copyright (c) 2021
 * 
 */


#ifndef _DRV8711_DRIVER_H
#define _DRV8711_DRIVER_H

// enable this define to configure the driver in a loopback mode
#define LOOPBACK_TEST


#include <stdint.h>
#include <string.h>
#include <unistd.h>
#include <stdio.h>
#include <stdlib.h>
#include <getopt.h>
#include <fcntl.h>
// #include <sys/ioctl.h>
#include <iostream>


extern "C" {
#include <sys/ioctl.h>
    #include <linux/types.h>
    #include <linux/spi/spidev.h>
}



#define _CONFIG_SPI_BITS_PER_WORD           16
#define _CONFIG_SPI_BAUD_RATE               500000

#define _SPI_LOOPBACK_ON                    1
#define _SPI_LOOPBACK_OFF                   0

// enum DRV8711_status;

enum ErrorCodes_Type
{
  _NO_ERROR,
  _SPI_INIT_FAIL_OPENDEV,
  _SPI_INIT_FAIL_MODE,
  _SPI_INIT_FAIL_BITS_PER_WORD,
  _SPI_INIT_FAIL_BAUD_RATE,
  _SPI_READ_FAIL,
  _SPI_WRITE_FAIL,
  _SPI_TRANSFER_FAIL
};


/*---------------- REGISTER ADDRESSES --------------------*/



class DRV8711_driver {
    
    private:
        int _addr;
        int _devId;
        int _drvStatus;
        int _spiFd;
        __u8 _spiChannel;
        __u8 _spiMode;
        __u8 _spiBitsPerWord;
        __u32 _spiBaudRate;

        
        auto _readByte(__s32 *data, __u8 addr) -> ErrorCodes_Type;
        auto _SPI_init() -> ErrorCodes_Type;
        auto _SPI_read(__u8 *rxBuf, __u32 rxBufCount) -> ErrorCodes_Type;
        auto _SPI_write(__u8 *txBuf, __u32 txBufCount) -> ErrorCodes_Type;
        auto _SPI_transfer(__u8 *rxBuf, __u8 *txBuf, __u32 bufCount) -> ErrorCodes_Type;

    public:        
        
        DRV8711_driver(__u32 spiChannel, __u8 spiMode, __u32 spiBaudRate, __u8 spiBitsPerWord);
        ~DRV8711_driver();

        auto setSpeed(__u8 speed) -> ErrorCodes_Type;

        

};



#endif

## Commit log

2020-12-30 initial setup for 3 DOF arm simulations. I need to rename the files. Current plan is to do a 3 DOF arm so i can get the hang of ros-gazebo sims and then move to 6 DOF
    [robarm.urdf.xacro]
2021-01-01 update to 3 DOF urdf - still very rudimentary. however, i will use this for testing some basic ROS code for now.
    [materials.xacro, robarm.urdf.xacro]
2021-01-14 spur_gear added
    [spur_gear.FCStd]
2021-01-14 adding stl
    [second_draft.stl]
2021-02-09 Add motor driver PCB init
    [motor_driver_prj.kicad_pcb, motor_driver_prj.sch]
2021-02-21 update PCB schematic
    [AllDrivers.sch, extConnectors.sch, motor_connectors.sch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]
2021-02-21 schematic complete?
2021-03-28 new part placements.
    [AllDrivers.sch, extConnectors.sch, motor_driver_prj.kicad_pcb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]
2021-04-15 restructuring code
    [materials.xacro, robarm.urdf.xacro]
2021-04-25 Motor Driver PCB rev 1
    Motor Driver PCB rev 1
    [530470310.stp, EE_SX1071.step, ZF5S-40-01-T-WT.stp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]
2021-04-25 gerber files for motor driver board v1.0
    [motor_driver_prj-B_Cu.gbl, motor_driver_prj-B_Mask.gbs, motor_driver_prj-B_Paste.gbp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]
2021-04-25 added pictures for motor driver board
2021-05-12 working 3 joint arm
    [robarm.urdf.xacro]
2021-05-17 update part list
    [partslist.xlsx]
2021-10-02 add code for SPI driver portion. Also, tested that it works fine

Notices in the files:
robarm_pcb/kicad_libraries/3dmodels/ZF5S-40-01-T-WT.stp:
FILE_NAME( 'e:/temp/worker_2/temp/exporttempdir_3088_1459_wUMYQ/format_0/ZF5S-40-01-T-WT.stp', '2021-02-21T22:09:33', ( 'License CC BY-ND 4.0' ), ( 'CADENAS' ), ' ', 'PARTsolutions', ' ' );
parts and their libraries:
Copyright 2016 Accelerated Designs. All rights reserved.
